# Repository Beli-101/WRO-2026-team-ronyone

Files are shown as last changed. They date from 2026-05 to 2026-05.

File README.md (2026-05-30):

# WRO 2026 Future Engineers -  RONYONE

## 📁 Table of Contents

- [👤👤👤 About the team](#the-team)
- [⚔️ Challenge Overview](#challenge-overview)
- [⚔️ Software Development Environment](#software-development-environment) 
- [🚗 Our Robot](#our-robot)
- [ 🤸 Mobility Management](#mobility-management)
    - [ Drive](#drive)
      - [ Motor](#motor)
      - [ Wheels](#wheels)
  - [Steering](#steering)
    - [ Steering Servo Motor](#servo-motor)
  - [Assembly](#assembly)
  - [Assembled](#assembled)

## THE TEAM
Our team is composed of three members David Beluhan, Gabriel Martinko, Vedran Barunčić and our mentor Rondald Galić. We have a goal of becoming true engineers but more importantly critical thinkers. The team has competed in WRO 2025, in the Future Engineers category (WRO Open in Ljubljana, Slovenia) and WRO 2024 in Future Innovators (WRO Open in Brescia, Italy).

        Vedran, age 16: programming
        Gabriel, age 16: 3d design
        David, age 15: 3d design

## CHALLENGE OVERVIEW

This is the game mat which we are gonna do all the challenges on:

OPEN CHALLENGE
For the open challenge, the robot just needs to do 3 laps around the map, and finish in the finishing zone.

OBSTACLE CHALLENGE
The obstacle challenge is a little bit more complicated. Esentially it has the same form as the open challenge, meaning that the robot still needs to do 3 laps around the map but now there are red and green pillars placed randomly on the map, if it is a red pillar the robot should go right around it, and if it is a green pillar it should go left around it. At the end of the 3 laps, the robot has a designated parking spot that you can see is colored pink, in the space the robot needs to parallel park.

## Software Development Environment

For efficiency, the software development was separated from the mechanical build. While the mechanical team worked on the physical robot, the software was developed and tested in Webots by Cyberbotics — an open source robot simulation application that provides a complete environment to model, program and simulate robots.

The first step was creating a new world in Webots, importing the WRO Future Engineers map scaled to real dimensions, and adding all track elements: pillars, parking space walls, outer walls and inner walls. This allowed full simulation testing without needing the physical robot.

The robot itself was initially built with standard differential drive, but we quickly realized there was no clean way to implement steering - only by creating speed differences between left and right wheels. This led us to rebuild the entire robot using the AckermannVehicle node, which is a dedicated module for Ackermann steering geometry. After inputting the correct physical dimensions and adding all sensors, we began testing.

### Sensors Used
| Sensor | Implementation | Purpose |
| --- | --- | --- |
| Camera “color sensor” | 1×1 camera, RGB read | Detects blue/orange lines on track |
| Camera | Standard detection camera | Detects red/green pillars on track |
| Front distance sensor | Standard distance sensor | Wall proximity during turns |
| Front-left distance sensor  | Standard distance sensor | Inner wall clearance (left turns)  |
| Front-right distance sensor | Standard distance sensor | Inner wall clearance (right turns) |
| IMU | Inertial measurement unit | Yaw tracking for turn control |
| Front camera | Camera (obstacle challenge) | Pillar detection and avoidance |
| Side sensors | Distance sensors (obstacle challenge) | Lateral positioning |
| Rear sensor | Distance sensor (obstacle challenge)  | Parking and reversing |

Since no dedicated color sensor node exists in Webots, a camera was used with resolution set to 1×1 pixels. Each frame, the red, green and blue channel values are read directly and classified by threshold ranges.

### Open Challenge - Control Logic
The open challenge controller runs a state machine with three mutually exclusive phases: turning, straightening, and cruising.
Color Detection
The 1×1 camera captures one pixel per timestep. The RGB values are compared against tuned threshold ranges to classify the floor color:
```python
if   40 < r < 80  and 50 < g < 90  and 100 < b < 150: detected = "blue"
elif 140 < r < 200 and 70 < g < 120 and 30 < b < 80:  detected = "orange"
else:                                                   detected = None
```
Blue indicates a left turn, orange a right turn. The first detected color also sets the direction for all subsequent turns in that run.

### State Machine
Cruising is the default state. While cruising, the robot continuously compares its current IMU yaw against the nearest 90° increment and applies a small fixed steering correction if the heading error exceeds 1.5°. This prevents small angular errors from accumulating over multiple laps.
Turning is triggered when a color line is detected. The turn direction is locked to the first color seen at the start of the run. Rather than targeting an absolute yaw angle which breaks at the 270°→360° boundary, the controller measures how many degrees have been rotated since the turn started:
```python
diff = angle_diff(yaw, turn_start_yaw)
turned_so_far = diff      # blue (left)
turned_so_far = -diff     # orange (right)
```
The turn completes after 87° of rotation, leaving a small margin to account for mechanical overshoot. During the turn, speed is dynamically adjusted based on front distance sensor readings to maintain safe wall clearance.
Straightening activates immediately after a turn finishes. The controller snaps to the nearest 90° heading as a target and applies a fixed ±0.15 radian steering correction until the heading error falls within 1.5°, at which point the wheels return to center.

Each time a color line triggers a turn, a counter increments. On a square track with one line per corner, three full laps equal 12 turns. On the 12th detection, the robot completes its final turn, drives forward a fixed number of steps to return to the starting position, then stops.

The controller runs at a 2ms timestep, giving approximately 500 control loop iterations per second. This is critical for reliable color detection at speed — at higher timesteps the robot can drive past the color strip between two consecutive camera reads.

Occasional missed detection at start: At simulation startup the color sensor sometimes fails to detect the first line, causing the robot to drive straight through it. We believe this is a simulation artifact related to sensor initialization timing and expect it to be less of an issue on the physical robot cycle times. If it persists, the controller loop will be further optimized.

A demonstration video of the Open Challenge simulation in Webots can be viewed [here](Videos/Open_challenge_simulation.mp4)

## OUR ROBOT
| TOP | BOTTOM |
|---|---|
| <p align="center"><b>Top</b></p> | <p align="center"><b>Bottom</b></p> |

| LEFT | RIGHT |
|---|---|
| <p align="center"><b>Left</b></p> | <p align="center"><b>Right</b></p> |

| FORNT | BACK |
|---|---|
| <p align="center"><b>Front</b></p> | <p align="center"><b>Back</b></p> |

# MOBILITY MANAGEMENT
We have decided to move with RWD ( Rear Wheel Drive - https://en.wikipedia.org/wiki/Rear-wheel_drive) and 4 wheel steering. We considered using a differential, but through some calculations we concluded that the speed difference on wheels would be small enough to consider. However, in this challenge, we need sharp turns, so we decided to use 4 wheel steering to help with that. 
  ## DRIVE
Considering the 4 wheel steering and RWD, we had to have one axle at which there is both steering and drive. We decided to solve that problem with a simple drive shaft (https://en.wikipedia.org/wiki/Drive_shaft). Ours looks like this: <br>
RWD 
RWD1 <br>
SHAFT<br>
It consists of MULTIPLE parts: 
  1)  Wheel Shaft <br>
    Wheel shaftdimensions-WHEEL <br><br><br>
    
 2) Drive Shaft <br>
   ZDRIVE ZDRIVE1 <br><br><br>
   
 3) Cube <br>
    BCUBEBCUBE1 <br><br><br>

Also, important is that we have two bewel gears in ratio 2:1 (wheel:motor), from which we get more speed. Considering that we have 256RPM on our motor, we will have 512RPM on the output, which results in the speed of around 9km/h after some calculations. 
Here are the gears:
<br>
GEARS
<br>
Small gear: <br>
MALI-GEAR
<br><br><br>
Big gear: <br>
GEAR-BIG

After finishing the drive shaft we added steer bearings, as we call them. WE designed them so that we can place a bought ball bearing ( THIS ONE: https://www.zjhoto.com/product-706ac-6x17x6mm-miniature-angular-contact-ball-bearing ) so that the drive shaft doesn't wobble in it's hole. They also have a little hook added on them which are used to steer. The steer bearing  looks like this: <br>
SBSA <br> <br><br>

All the joints that are meant to be rotatible are 3mm in diamter, so that the M2 screw leaves enough space for rotating, but the top part od the screw and nut don't allow movement up and down. 

## MOTOR
| MOTOR | **FAGM25 - 370** |
|---|---|
| **Model:** FARF - 370 - 15 370  | **Voltage:**  12V |
| **No-load Speed:** 5600 RPM | **No-load Current:** 300mA |
| **Stall Torque:** ~1.716 Ncm | **Stall Current:** 900mA |
|  [Specs](https://www.foneacc-motion.com/upload/GM25-370.pdf) | **Function:** Drives the robot |

**Why we chose it?**
- previously available to us
- sufficient torque

To hold the motor in the place, we designed this holder: <br>

Motor-HOLDER

  # WHEELS
  The wheels construction will go like this: on the 3d printed solid part we will mount the also 3d printed but ____ material which will grip with the board like a tire. <br> <br><br>
  **INNER SOLID REAR WHEEL**  <br>
  

  **INNER SOLID FRONT WHEEL** <br>
  Front wheel is going to be a litlle different beacuse on the rear axle we have a bearing just before the wheel mounting so that the driveshaft and the wheel don+t wobble, but on the front axle, we don't have that so it is going to be on the wheel directly. The bearing is the same as the one on the rear axle.<br>
   <br>

  **OUTER RUBER PART OF THE WHEEL**
The first two parts shown are going to be solid, but that wouldn't be that great to go against the map, so we designed a outer part that is going to  be printed from the TPU material, and assembled to the inner parts. We aproximated that the friction coefficient would be around 0,8, and with that and the mass of the robot which we got from adding all the masses of components and calculating the volume of the 3d parts, multiplying by the material density, we got how much the frictin force would be, and it would be around 7,1N. That was also a comfirming factor of 2:1 ratio. <br>

OUTER-WHEEL

# STEERING
4 wheel steering means we needed an inversion so that axles dont rotate in the sam direction. If we want to go left, the front axle has to be rotated to the left, but the rear one to the right. The steering looks like this: It is located on the bottom side of our platform. <br> <br><br>
<br><br>
The steering consists of 4 parts: Steering gear, inverted steering gear, pivot arms and wheel holders.
So we divided the steering director in two parts: one is directly rotated by servo and the other is rotated by the first one. Looks like this:   <br><br><br>

1) Directly rotated from the servo:



<BR><BR>2) Inverted steering gear - rotated by the other gear: <br><br>

 <br>

<BR><BR>3) Pivot arm: <br><br>



<BR><BR>4) Wheel Holders: <br><br>



# SERVO MOTOR
## MOTOR
|| **80KG servo** |
|---|---|
| **Model:** SCX61  | **Voltage:**  6V|
| **Idle current:** 3mA | **Signal type:** PWM |
| **Stall current:** ~2.4A | **Torque:** 12.1kg-cm |
|  [Specs](https://www.aliexpress.com/item/1005008753027913.html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) | **Function:** Steers |

**Why we chose it?**
- previously available to us
- reliable
- more than strong enough

## CABLE MANAGMENT

At WRO 2025, our cable management system was a disaster, so this year we decided to take the situation seriously. We built custom component holders in which we built holes and tunnels specifically for the wires. Some of our holders have multiple holes so we can chose in what direction will wires go after the robot is put together.

TOF SENSOR HOLDERS

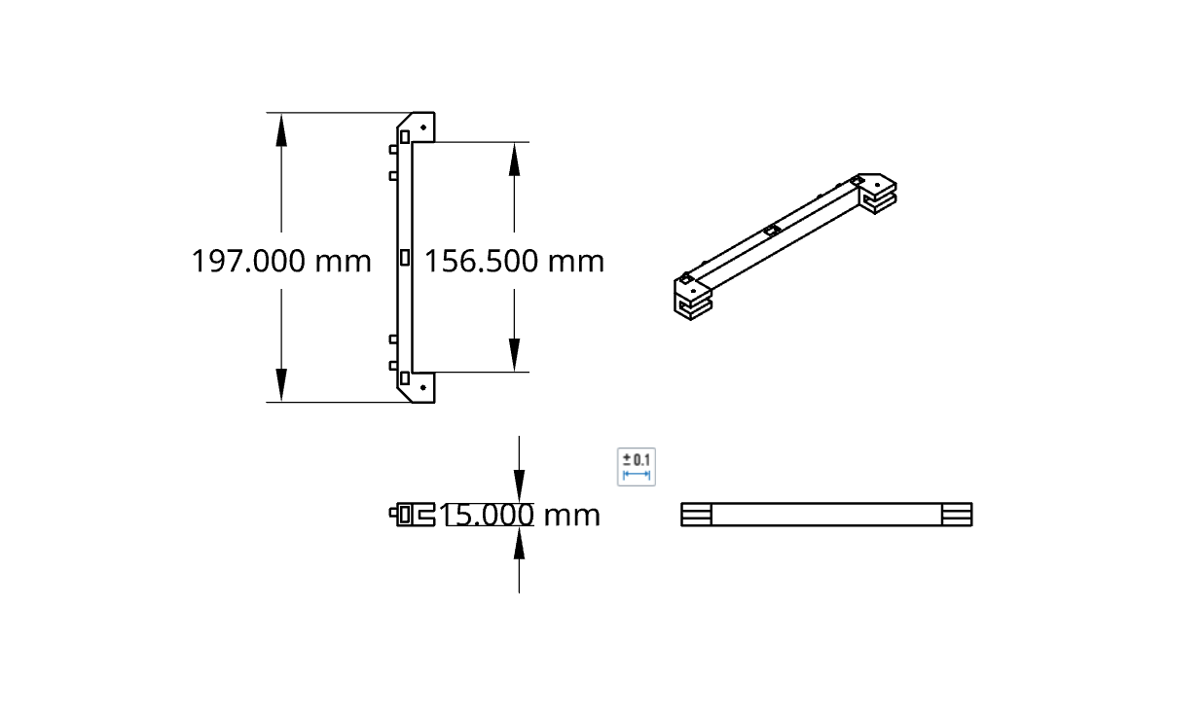
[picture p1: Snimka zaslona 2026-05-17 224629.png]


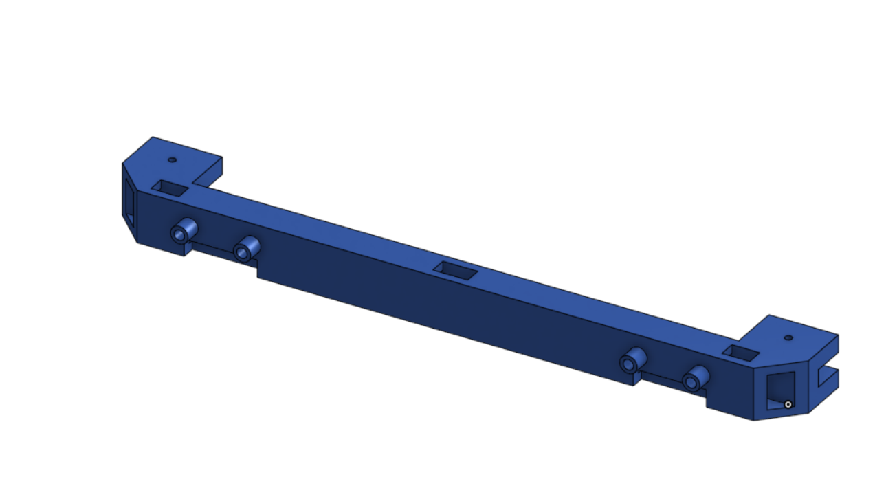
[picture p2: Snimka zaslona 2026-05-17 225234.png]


FRONT SENSOR HOLDER

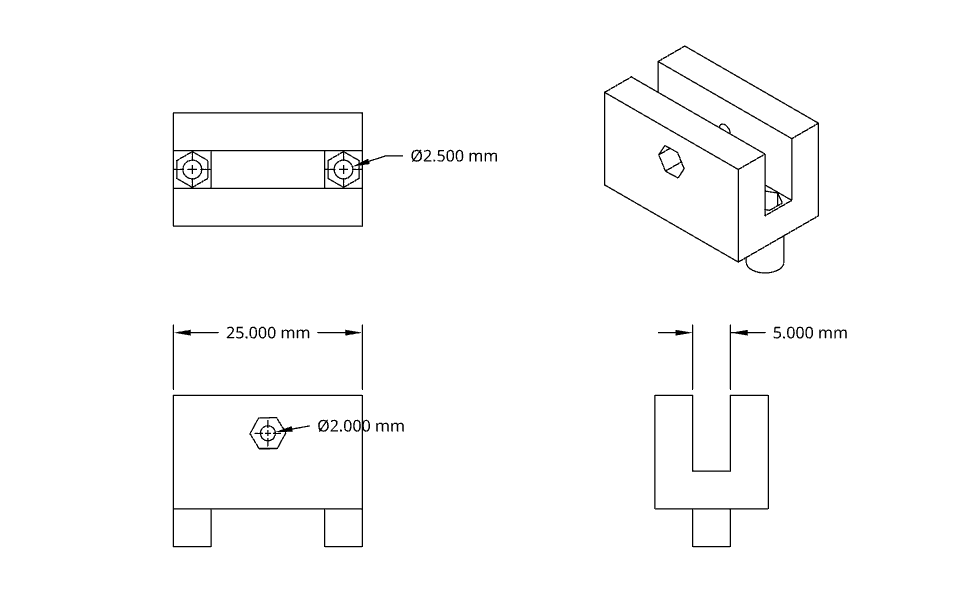
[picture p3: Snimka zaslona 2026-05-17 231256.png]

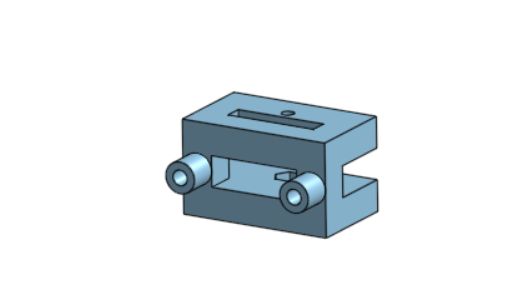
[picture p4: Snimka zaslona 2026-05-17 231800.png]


REAR SENSOR HOLDER

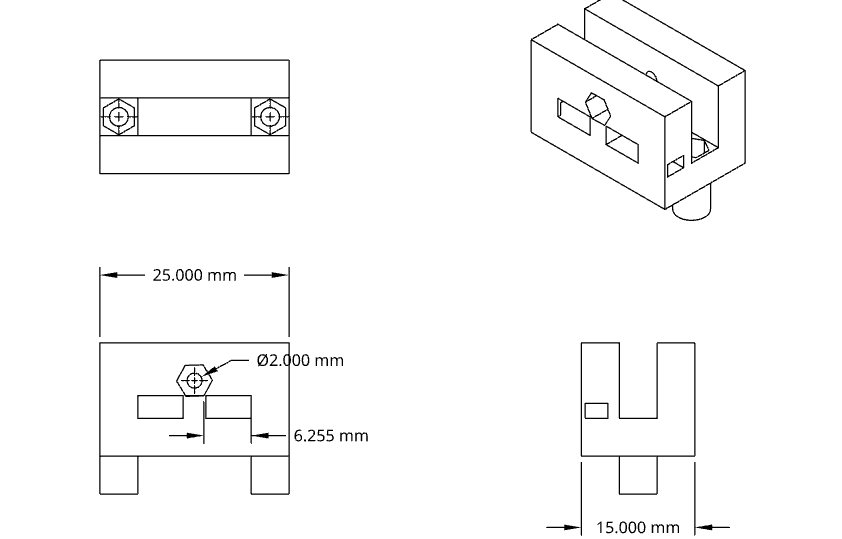
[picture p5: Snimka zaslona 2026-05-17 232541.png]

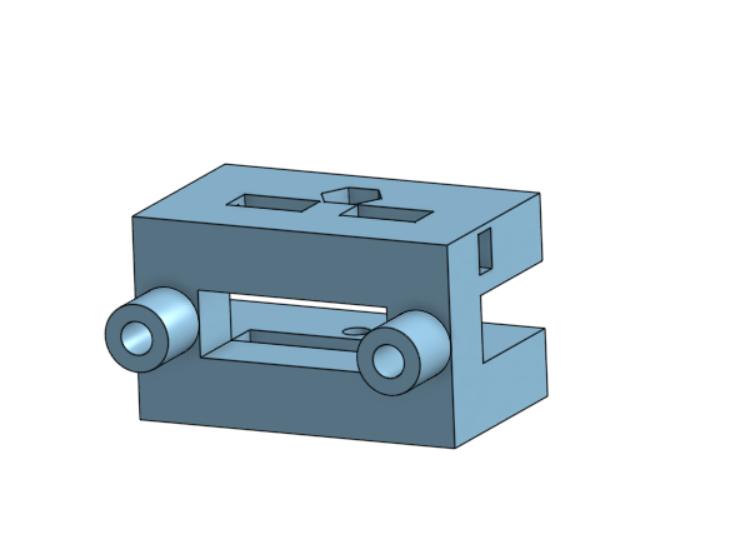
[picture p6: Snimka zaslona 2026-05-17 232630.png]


## Assembly

Both the drive and steering system, are pinned up up to the chasis using holders using M2 screws and bolts. 
The chasis looks like this: <br>

<br><br><br>

The connectors look like this: <br>
THE FRONT ONE: <br>

 <br><br>

THE REAR ONE: <br>

This one had to be different because of the big gear which would get in the way. <br> 


HOLDER-REAR

And here is everything:


## Assembled
        pictures of robot really connected

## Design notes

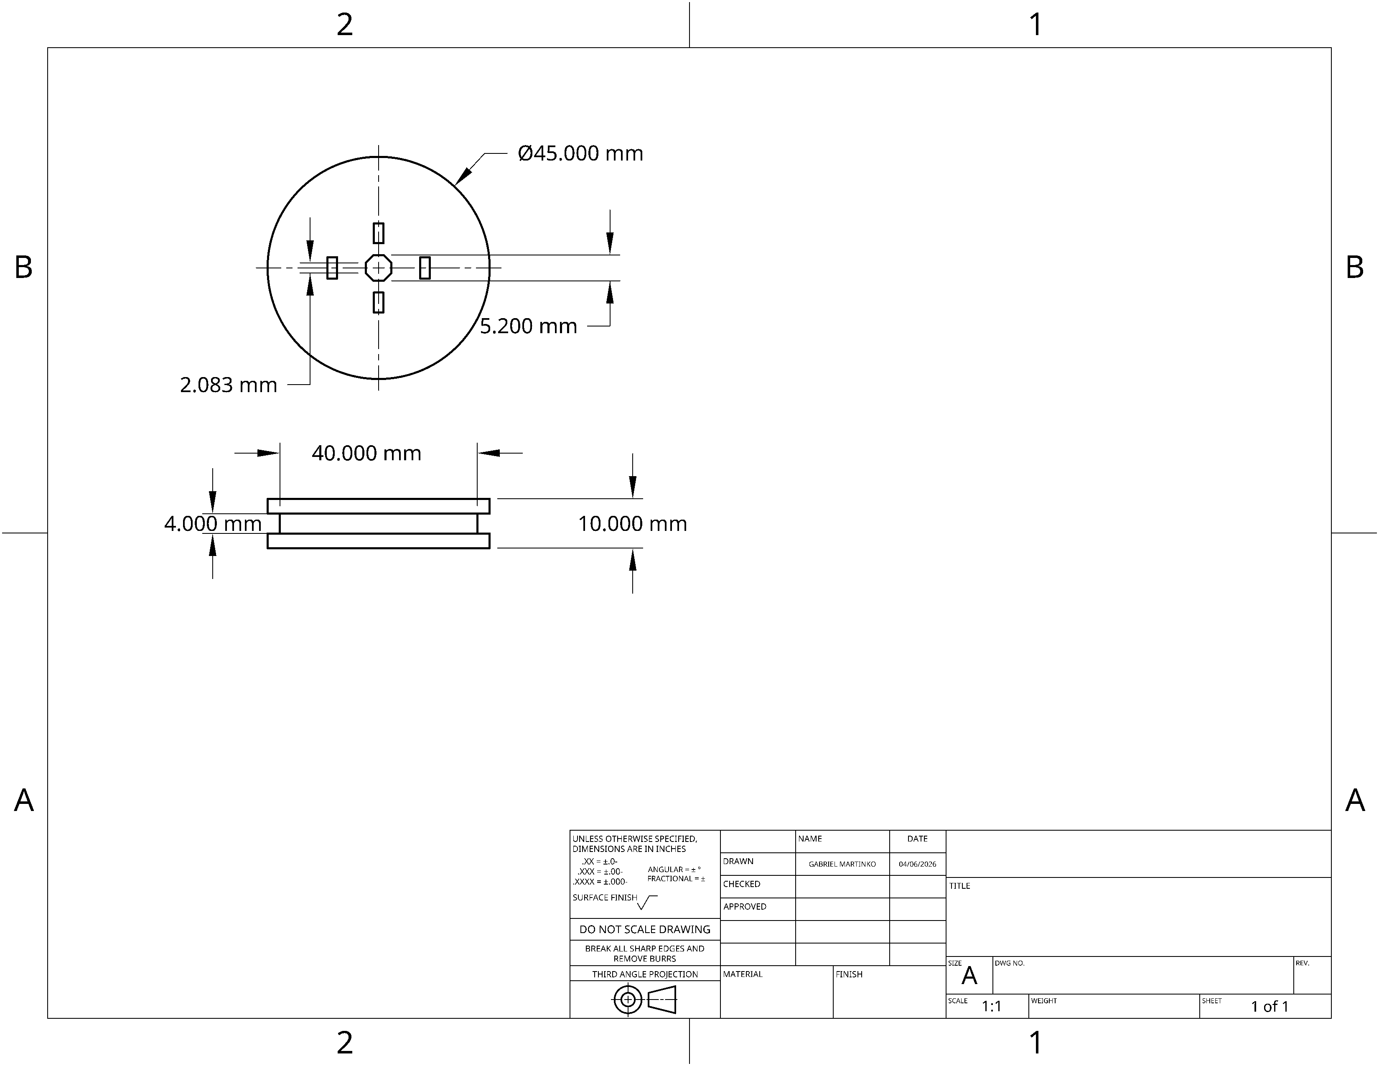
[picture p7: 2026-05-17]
Schemes/Connector FRONT.png

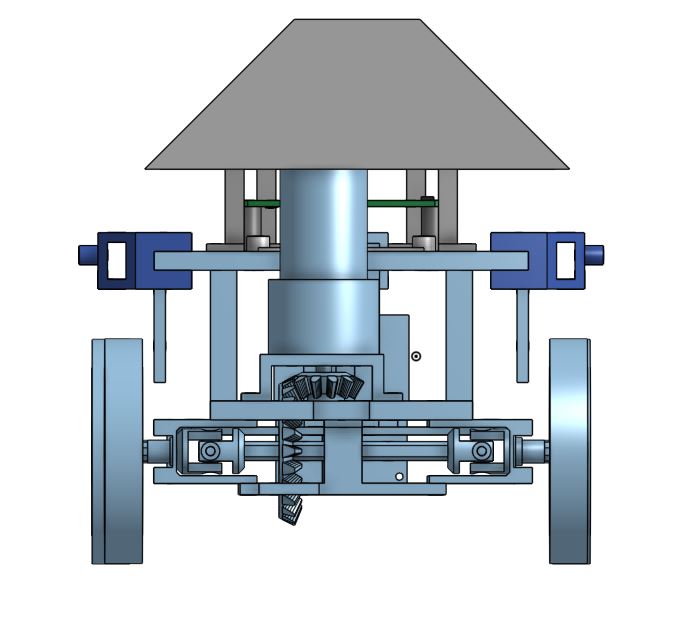
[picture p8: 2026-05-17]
Vehicle photos/BACK.JPG

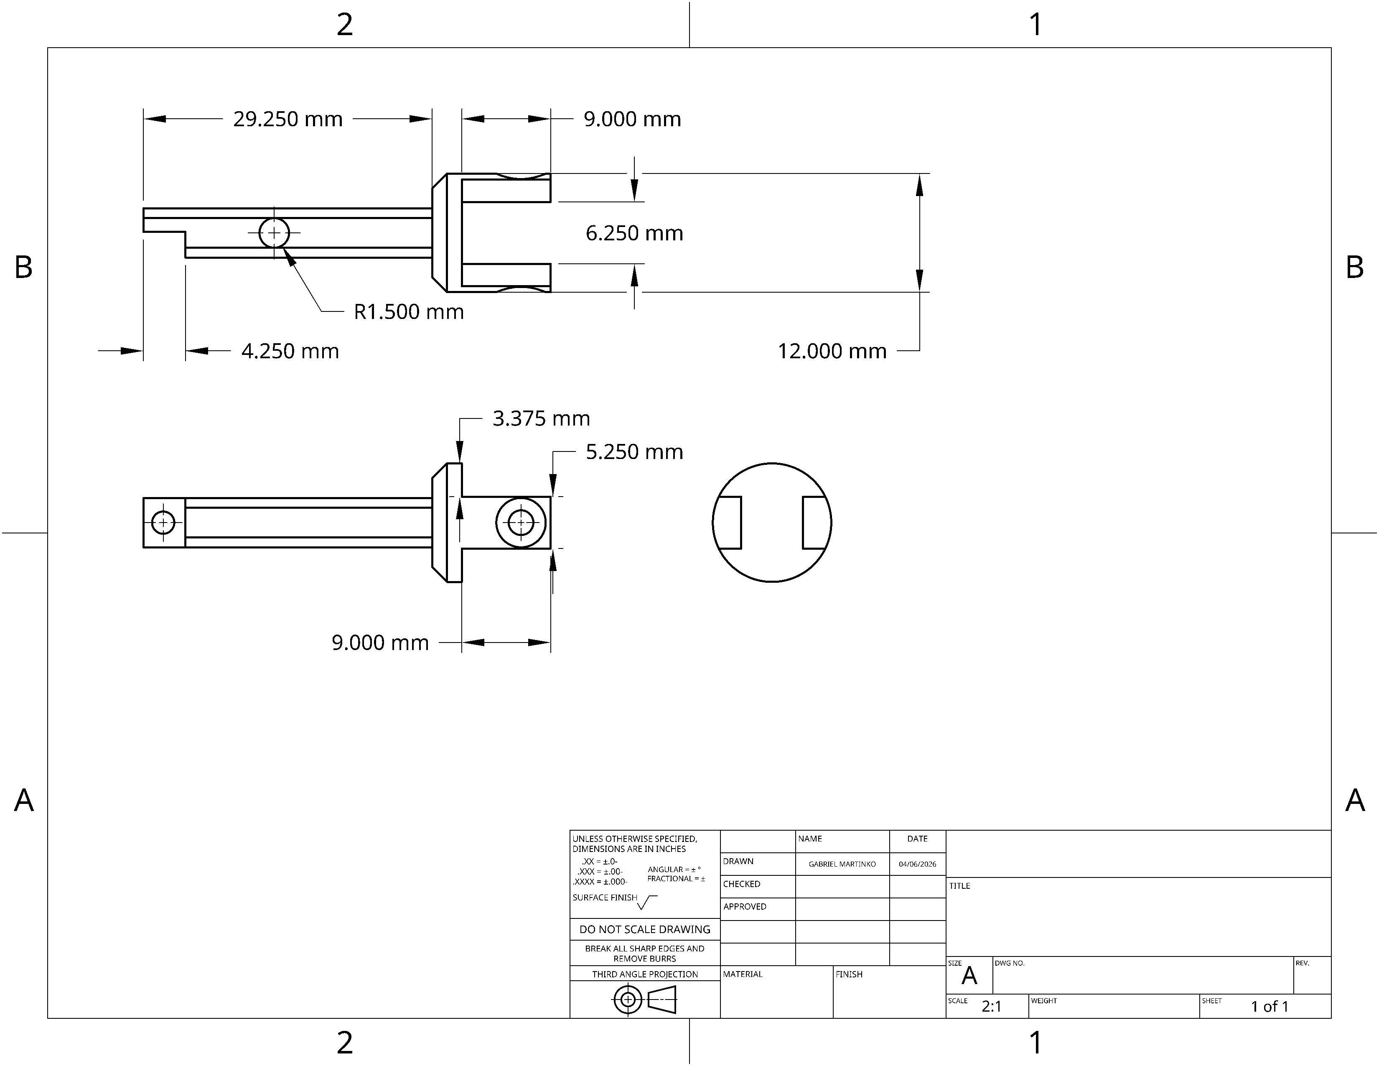
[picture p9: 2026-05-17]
Schemes/Drive Shaft.png

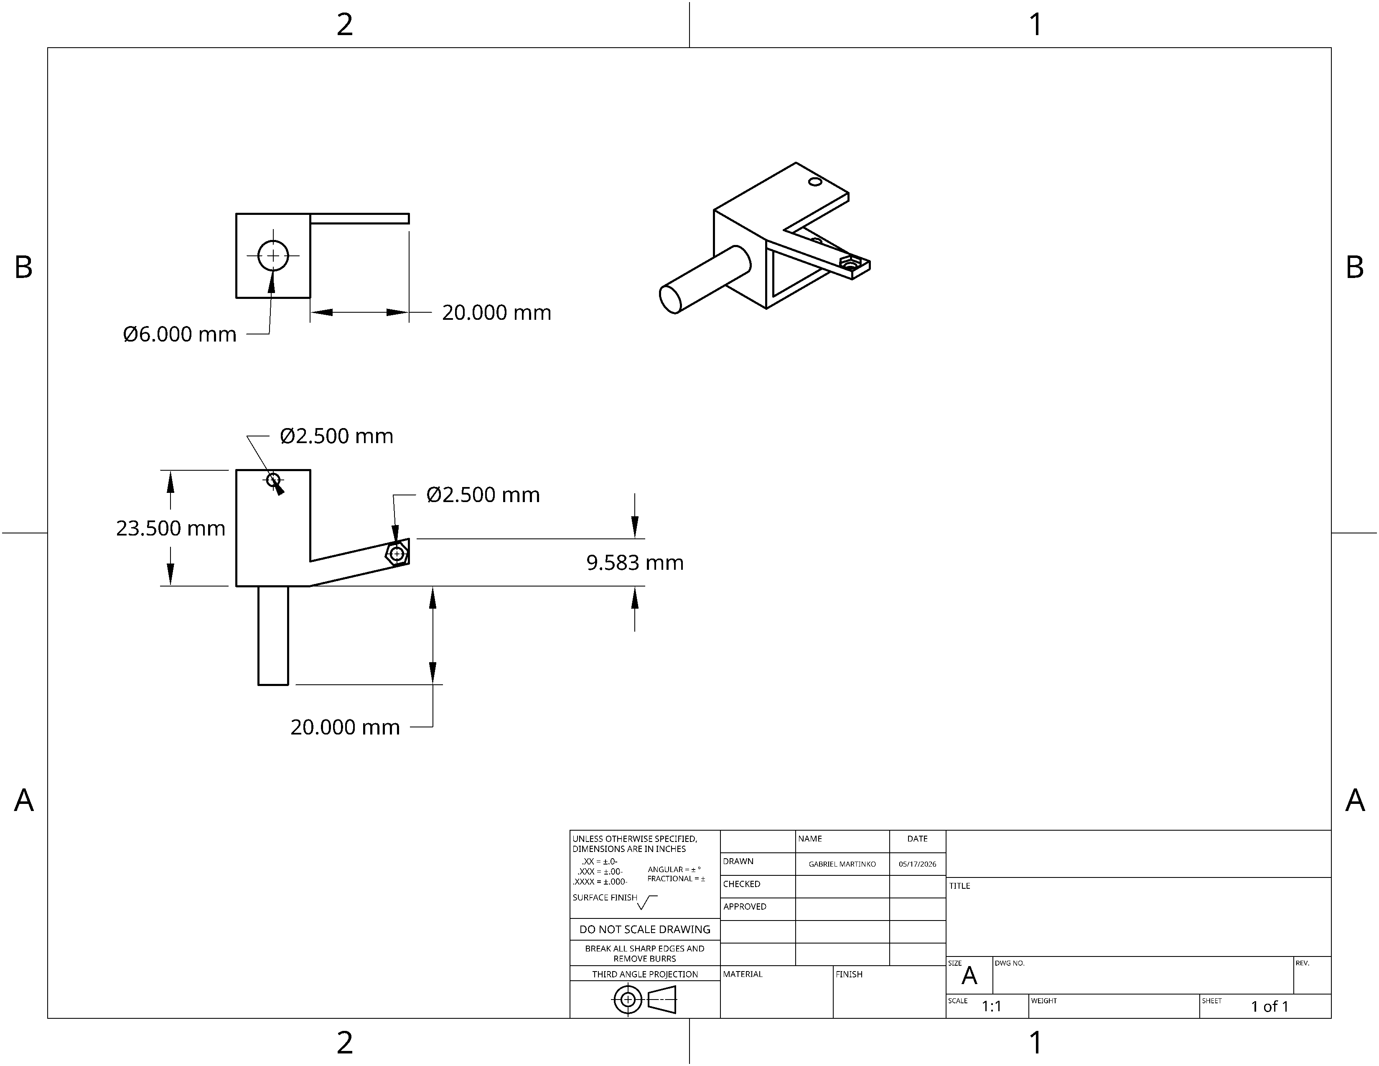
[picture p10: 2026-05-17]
Schemes/Steer Ležaj FRONT.png

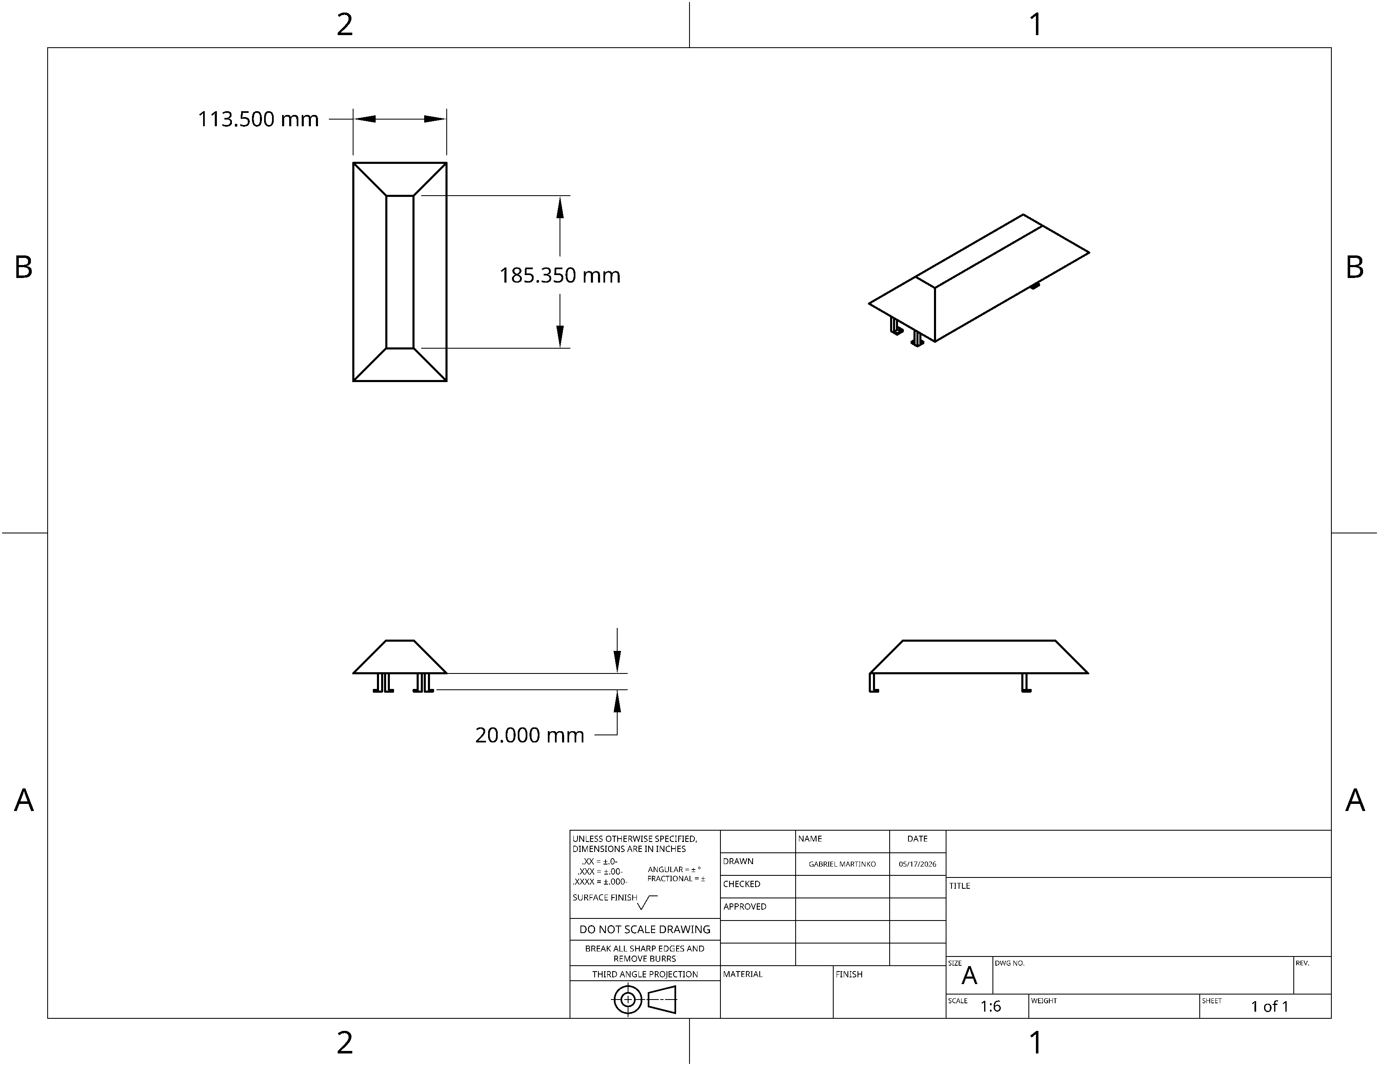
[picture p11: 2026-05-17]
Schemes/Poklopac.png

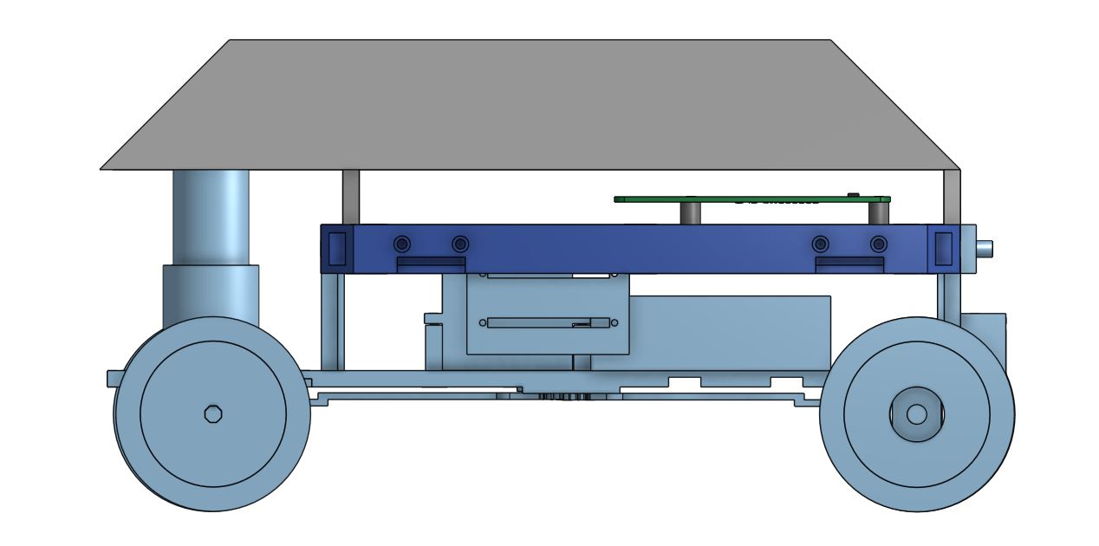
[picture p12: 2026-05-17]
Vehicle photos/RIGHT.JPG

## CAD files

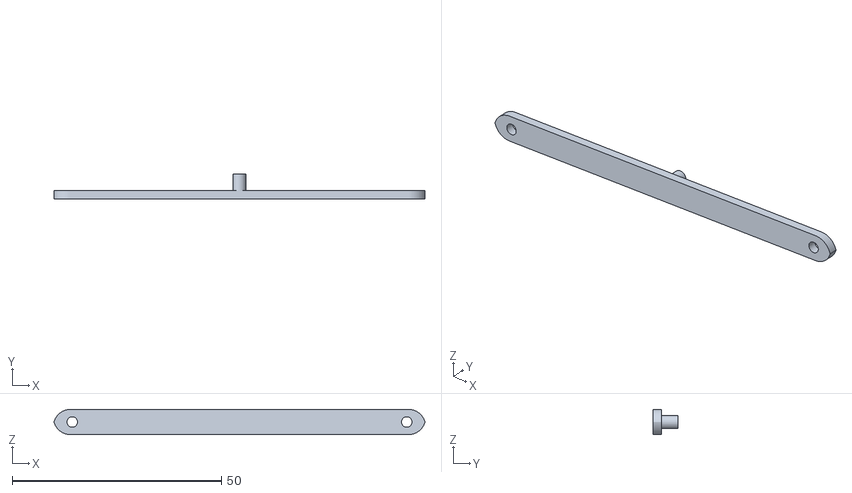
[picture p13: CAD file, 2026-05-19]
3D FILES /FRONT/Pivot Arm (N).stl
88.7 x 6.00 x 6.00

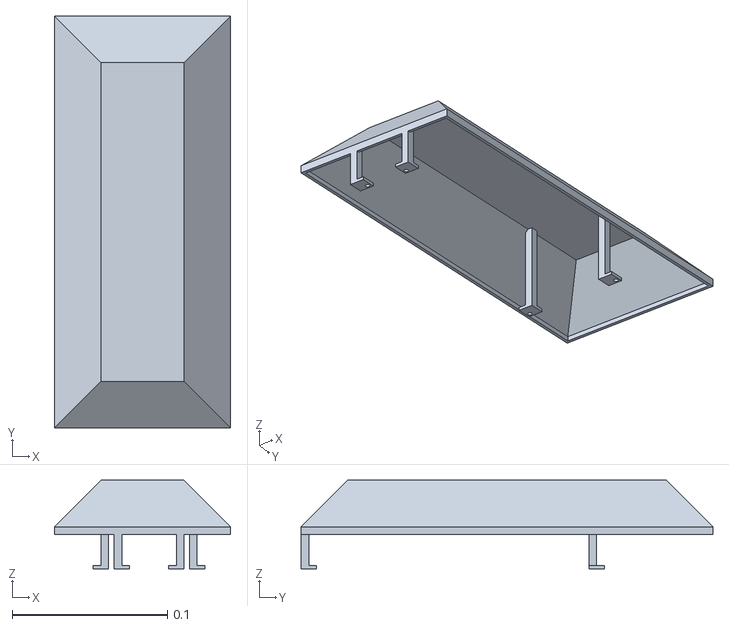
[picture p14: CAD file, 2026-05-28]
3D FILES /PLATFORM/poklopac.stl
0.113 x 0.265 x 0.057

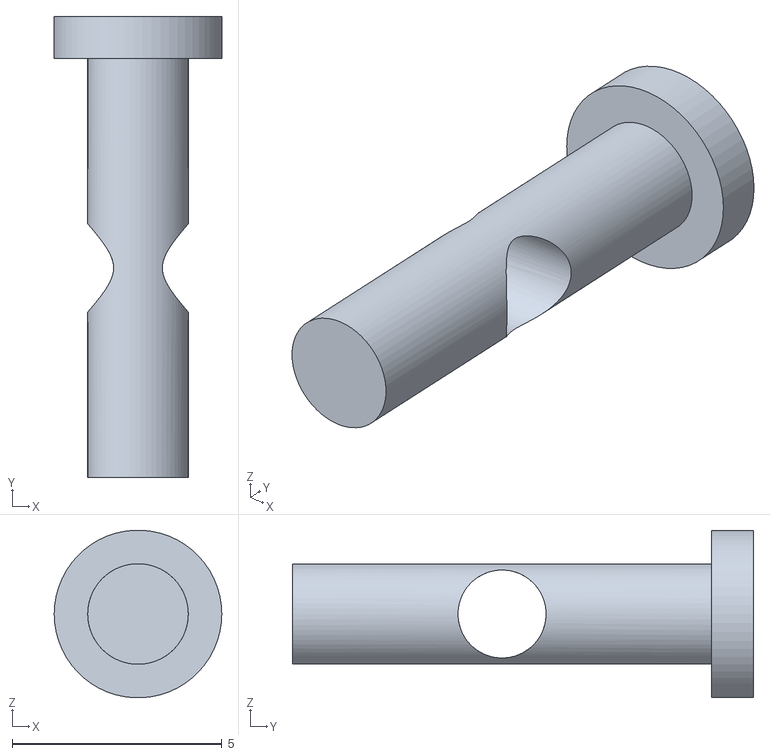
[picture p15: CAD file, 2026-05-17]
3D FILES /REAR/Pin Cube.stl
4.00 x 11.0 x 3.99

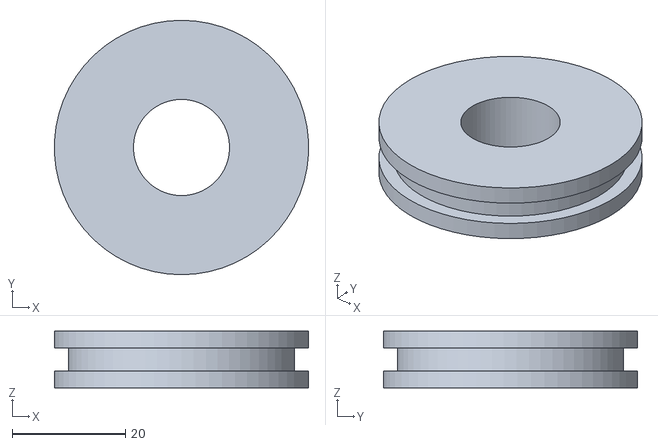
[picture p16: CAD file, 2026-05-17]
3D FILES /FRONT/KOTAČ STEER.stl
44.9 x 45.0 x 10.0

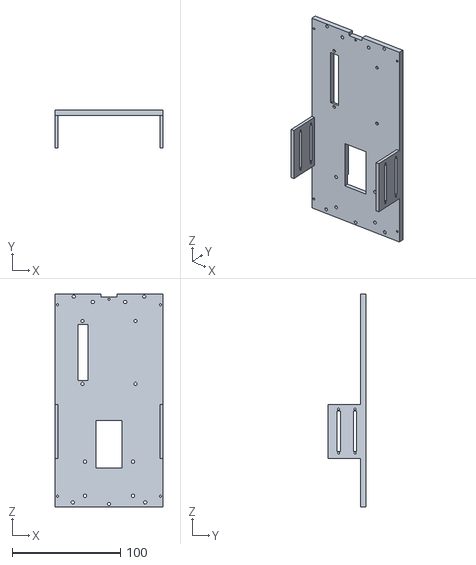
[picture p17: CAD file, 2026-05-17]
3D FILES /PLATFORM/Platform - KAT.stl
100.0 x 35.0 x 197.0

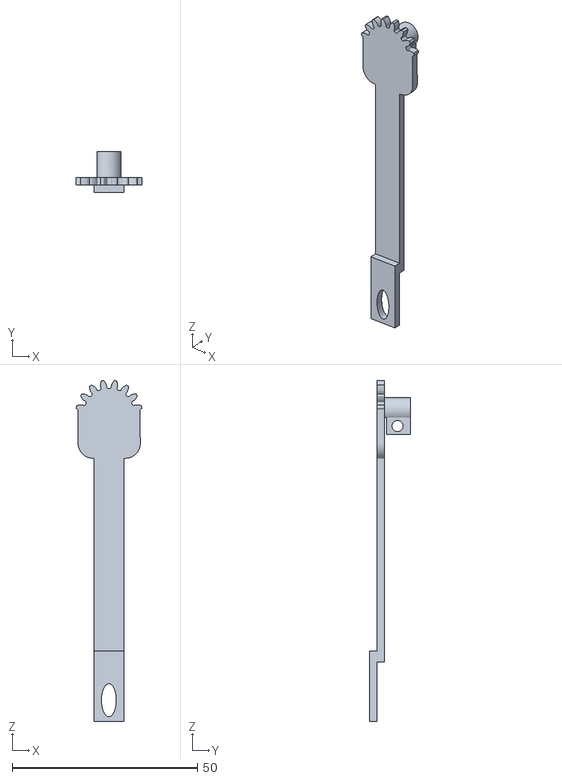
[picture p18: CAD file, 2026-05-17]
3D FILES /FRONT/Inverted Steering Gear.stl
17.8 x 11.0 x 92.0

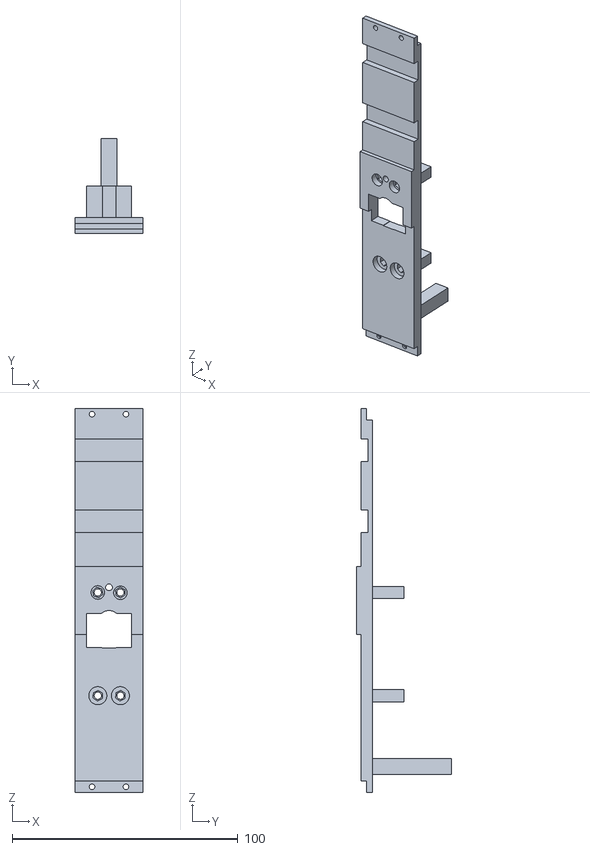
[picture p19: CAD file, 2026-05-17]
3D FILES /PLATFORM/Podvozje MIDDLE.stl
30.0 x 42.0 x 170.0

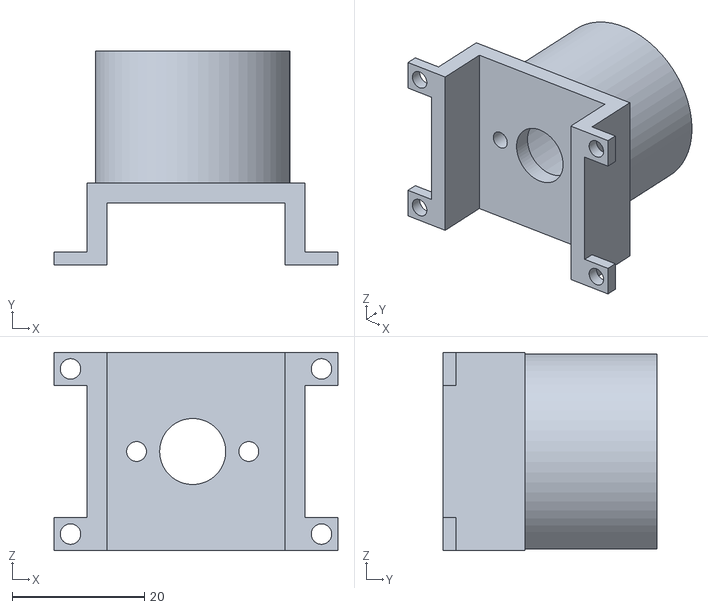
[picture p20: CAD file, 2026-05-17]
3D FILES /REAR/Motor Holder.stl
43.0 x 32.4 x 30.0

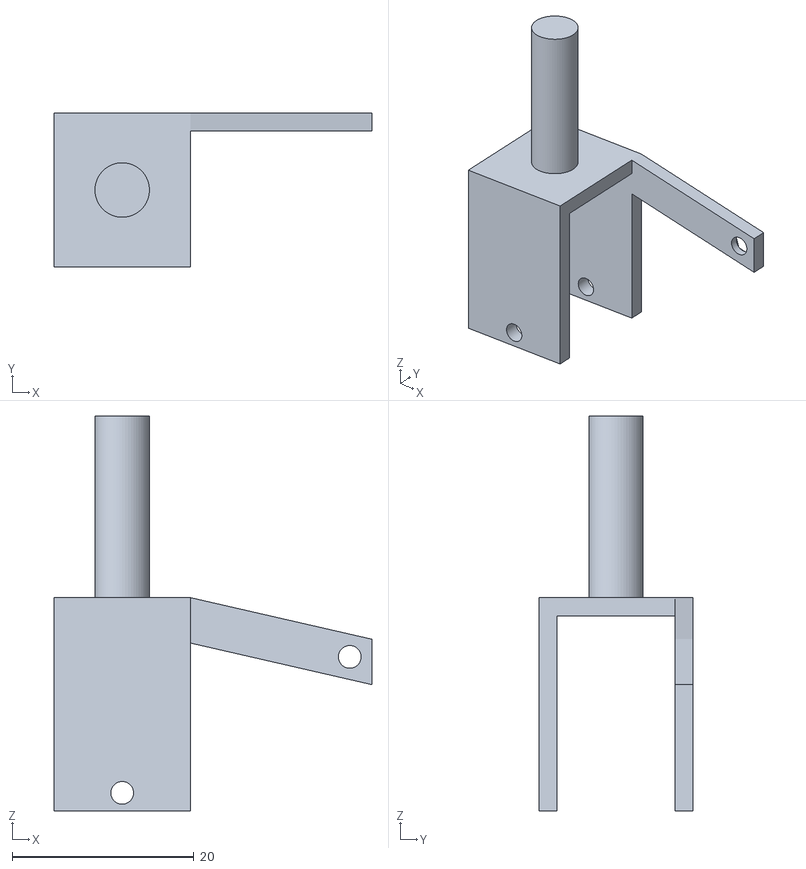
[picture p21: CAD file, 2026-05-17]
3D FILES /FRONT/Steer Ležaj FRONT LEFT.stl
35.0 x 17.0 x 43.5

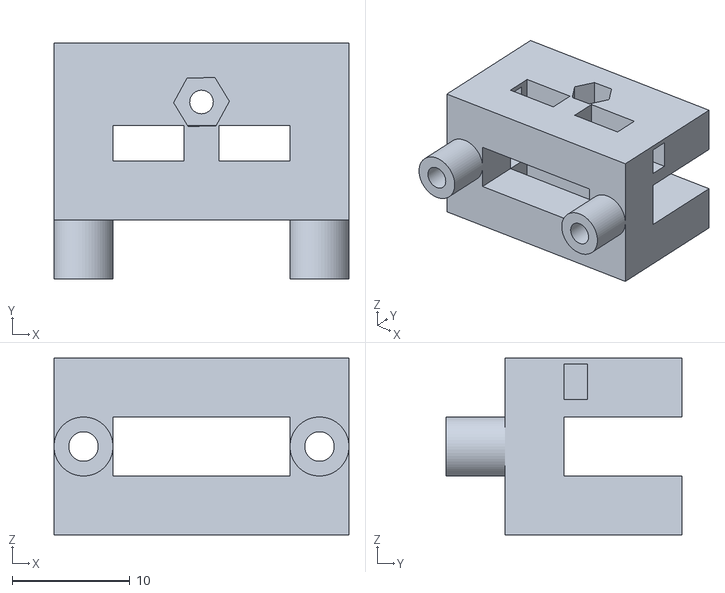
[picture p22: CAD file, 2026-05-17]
3D FILES /PLATFORM/FRONT & REAR Tof Sensor Holder.stl
25.0 x 20.0 x 15.0

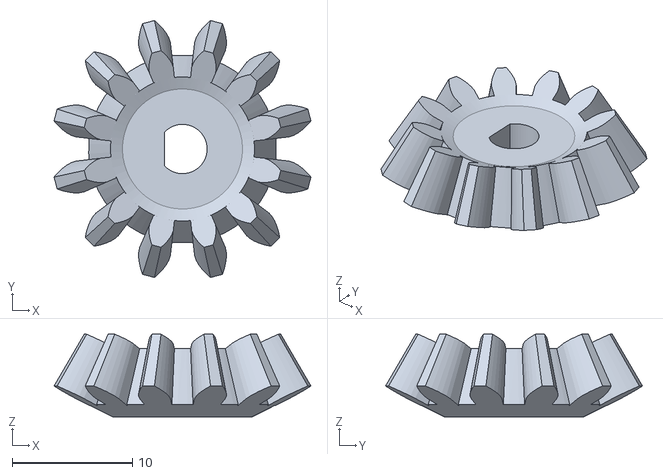
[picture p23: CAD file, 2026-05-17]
3D FILES /REAR/Smaller Bewel Gear.stl
21.4 x 21.4 x 6.87

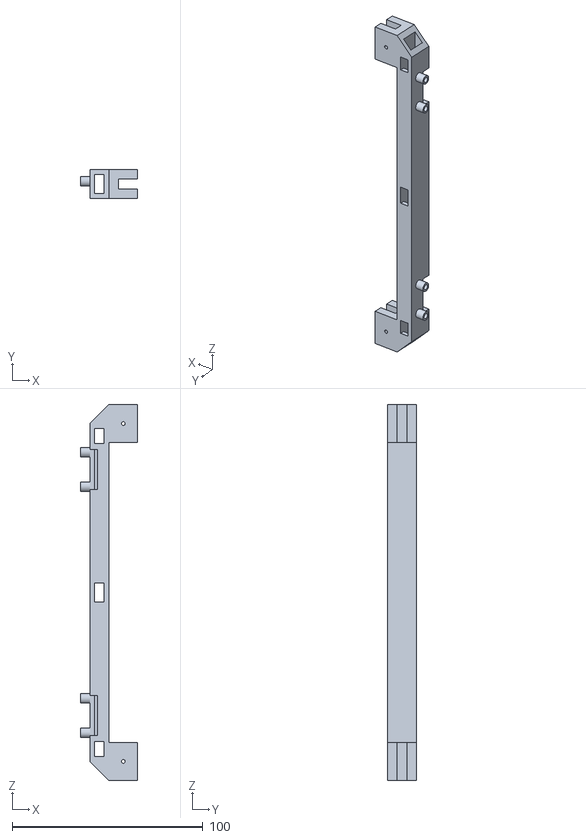
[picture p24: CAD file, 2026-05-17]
3D FILES /PLATFORM/SIDE ToF Sensor Holder.stl
30.0 x 15.0 x 197.0

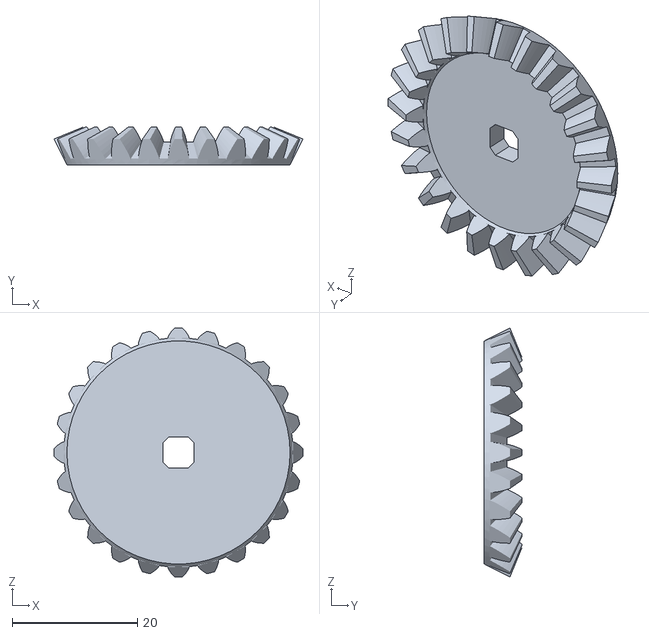
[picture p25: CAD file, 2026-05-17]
3D FILES /REAR/Bigger Bewel Gear.stl
39.7 x 6.03 x 39.7

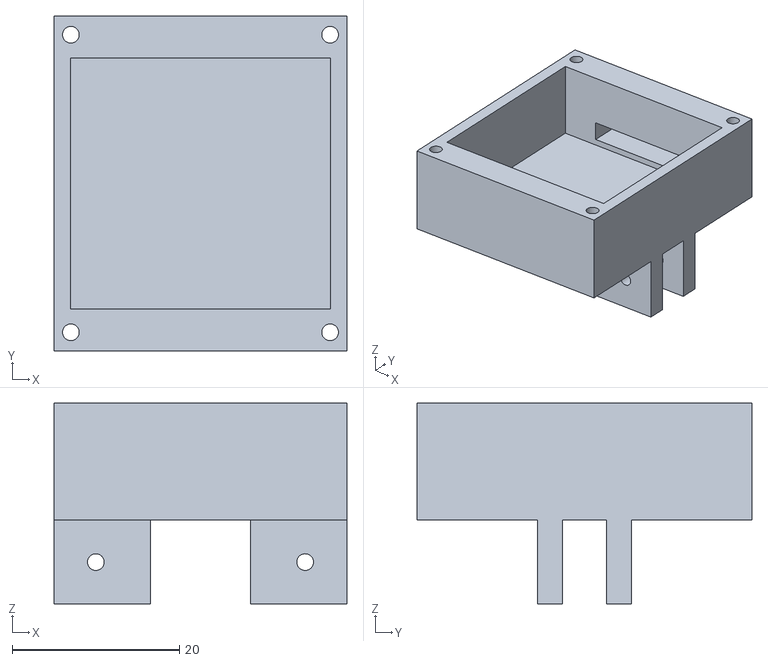
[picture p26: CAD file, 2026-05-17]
3D FILES /FRONT/Camer Holder.stl
35.0 x 40.0 x 24.0

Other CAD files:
3D FILES /REAR/KOTAČ DRIVE.stl
3D FILES /FRONT/Steer Ležaj FRONT RIGHT.stl
3D FILES /PLATFORM/Motor Driver Holder.stl
3D FILES /REAR/Drive Shaft.stl
3D FILES /FRONT/Connector FRONT.stl
3D FILES /FRONT/Podvozje FRONT.stl
3D FILES /FRONT/Steering Gear.stl
3D FILES /PLATFORM/Rasp Holder.stl
3D FILES /REAR/Connector REAR.stl
3D FILES /REAR/Cube.stl
3D FILES /REAR/Podvozje REAR.stl
3D FILES /REAR/Steer Ležaj REAR RIGHT.stl
3D FILES /REAR/Steer Ležaj REAR.stl
3D FILES /REAR/TPU GUMA.stl
3D FILES /REAR/Wheel Shaft.stl

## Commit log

2026-05-15 Software/Simulation Part Added
    Explained challenges, explained used sensors, explained code logic.
2026-05-17 Enhance README with cable management and sensor holder info
    Added sections on cable management and sensor holders to improve documentation.
2026-05-17 Update README with images and cable management section
    Added images for cable management and sensor holders.
